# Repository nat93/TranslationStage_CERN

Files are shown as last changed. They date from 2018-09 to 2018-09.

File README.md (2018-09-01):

# TranslationStage_CERN
> Software for linear motorized stages developed at CERN for UA9 experiment. Graphic User Interface based on Matlab and Arduino code for microcontrollers. There are 3D drawings of the stages created in SolidWorks.

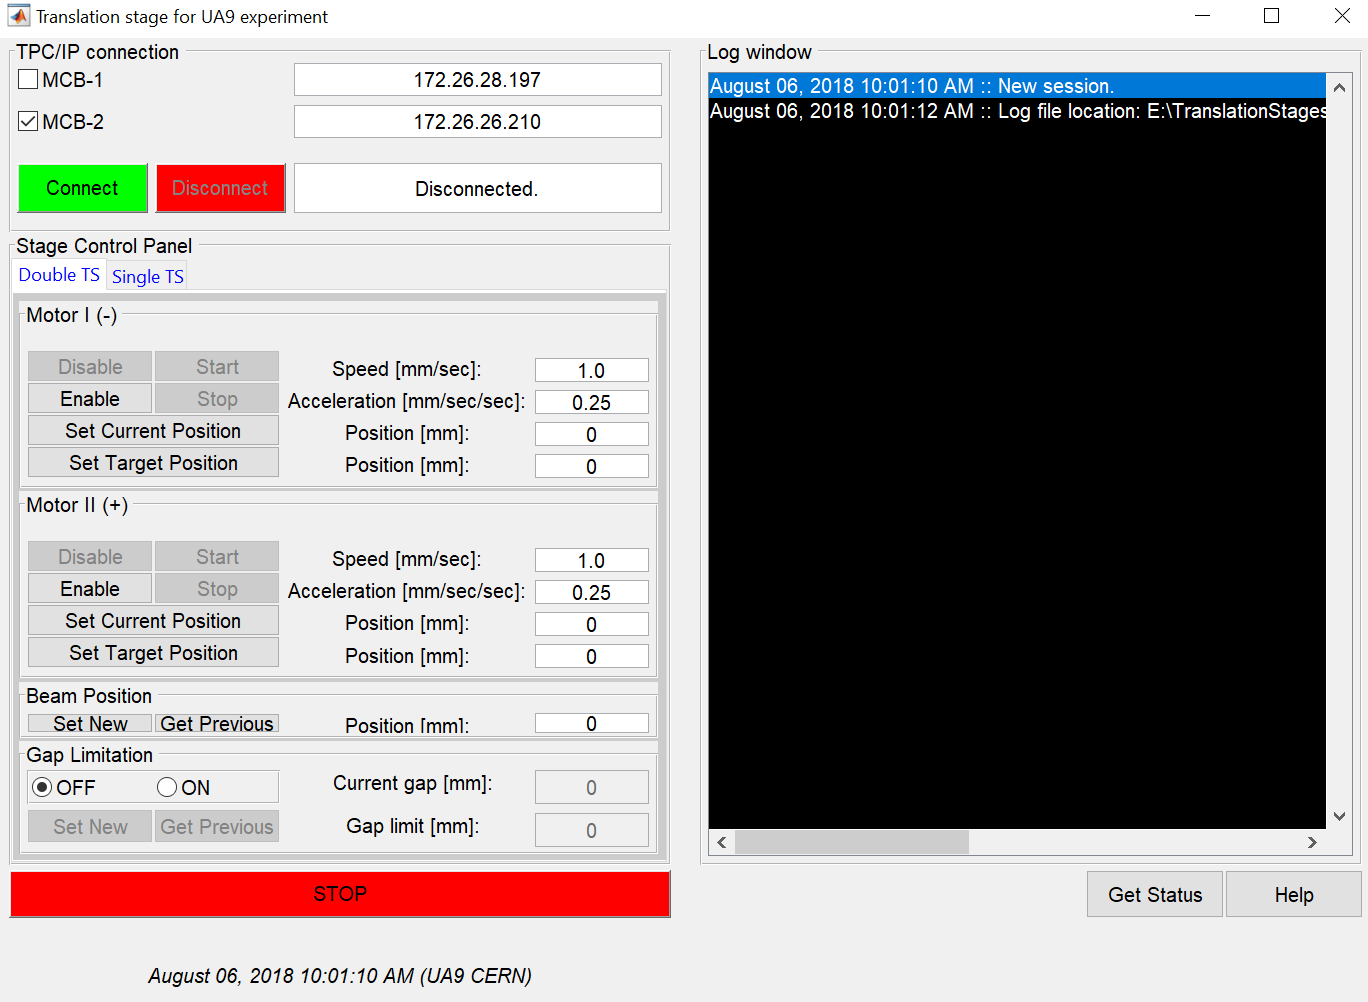
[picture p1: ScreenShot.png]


In recent times, an interest in the use of the bent crystals for the high-energy particle beam collimation and extraction has increased. A significant contribution to the technological progress of the development and installation such crystals at accelerators was made by the UA9 collaboration. So far an experimental work is carried out for the characterization of the crystals, their production and use on such accelerators as SPS or LHC at CERN. Nevertheless, before using the crystal for its intended purpose, it must be checked: determine the angle of the deflection, the efficiency of the channeling etc. Such tests are conducted at H8 SPS extraction beam line.

One of the important characteristics of the crystal is the probability of the inelastic nuclear interactions (INI) and its dependence on the crystal orientation with respect to the beam direction. To register the INI happening in the crystal a couple of plastic scintillators (10 × 25 × 5 mm3 ) is used in coincidences mode. For more effective INI events registration the position of the detectors should be symmetrical with respect to the center of the beam. 

Until 2017 the UA9 collaboration manually installed the plastic scintillators on the beam, each time interrupting the operation of the extraction line. This regime of the work was laborious and took a lot of experimental time. Thus, it was decided to create motorized linear platforms for moving the plastic scintillators with the possibility of remote control. In this case, physicists would not have to stop the work of the extraction line, and also remotely carry out calibration and alignment of the detectors with respect to the beam direction.

Description:
>> GUI_installer -- graphic user interface installation files for LINUX and WINDOWS operational systems.
>> TranslationStage_ARDUINO_SOURCE -- an Arduino based script for microcontroller.
>> TranslationStage_MATLAB_SOURCE -- a GUI script based on MATLAB.
>> TS-1 3D-CAD -- 3D model of the single translation stage.
>> TS-2 3D-CAD -- 3D model of the double translation stage.

Single Translation Stage:
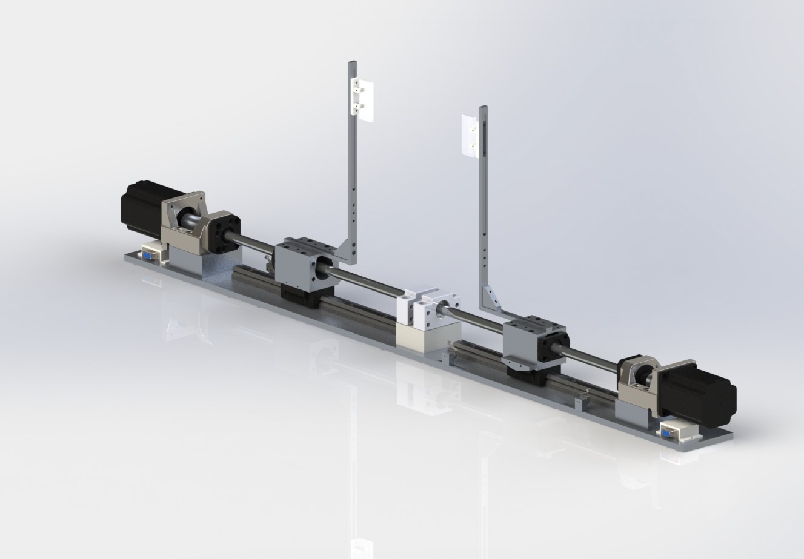
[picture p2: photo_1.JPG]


Double Translation Stage:
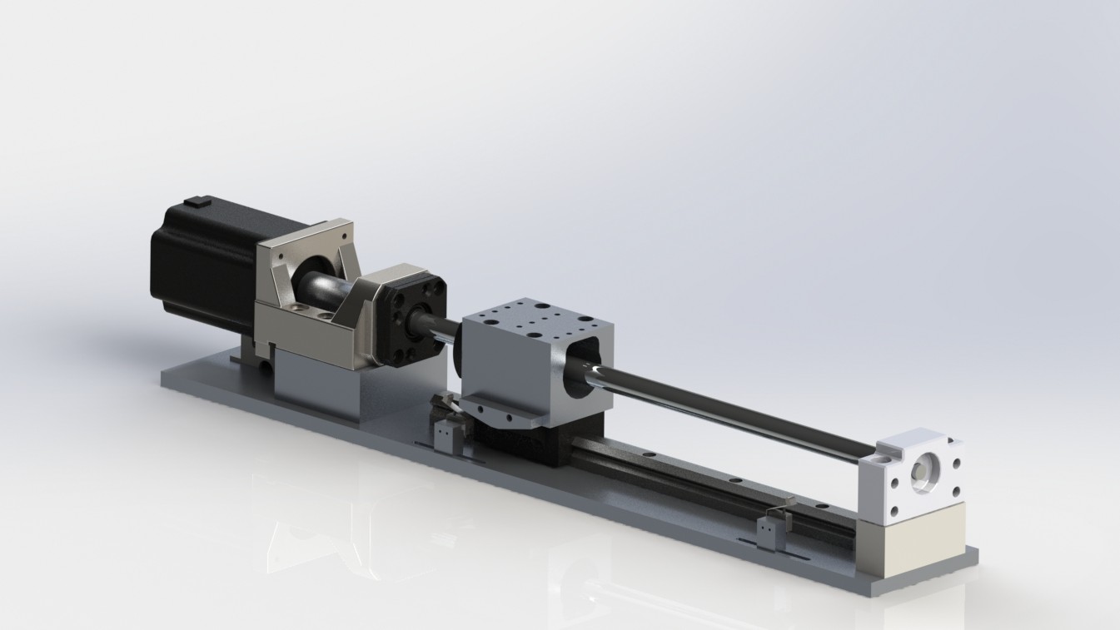
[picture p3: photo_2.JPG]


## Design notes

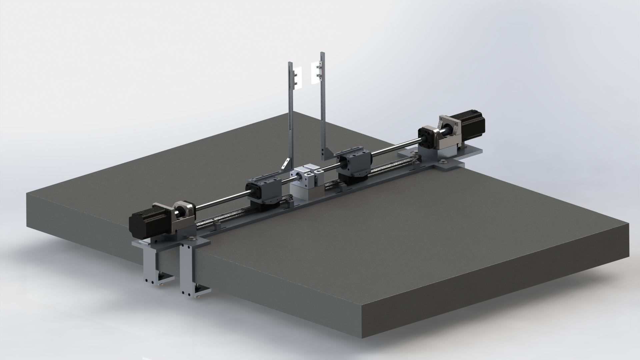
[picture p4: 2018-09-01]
TS-2 3D-CAD/pictures/photo.JPG

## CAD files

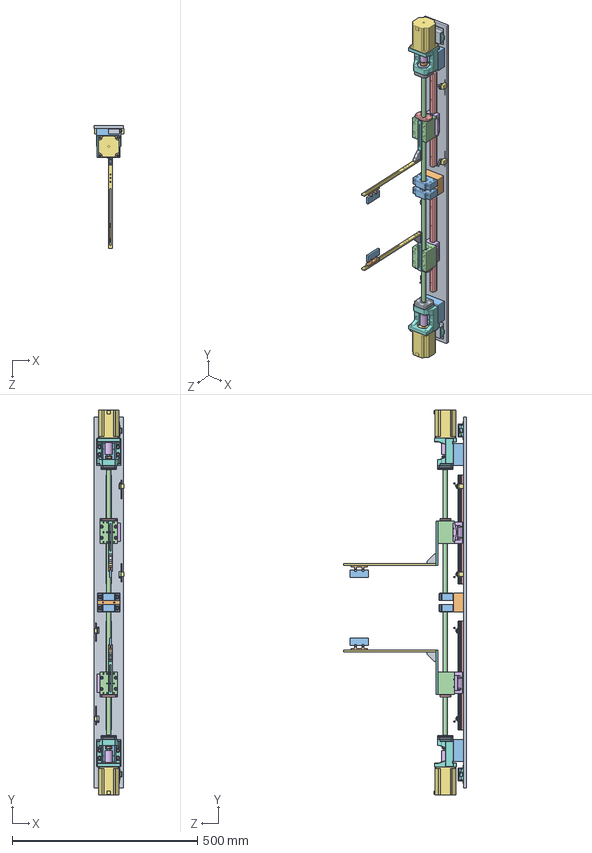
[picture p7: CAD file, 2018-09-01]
TS-2 3D-CAD/assembly.SLDASM
81.5 x 1038.2 x 332.0 mm
base_plate
support_1
BF10_C7 x 2
R1204_C7_ballscrew x 2
1204_FSKD x 2
BF_25D34L_Flexible_coupling x 2
NEMA23_SY57STH76_4004A x 2
MBA10-C x 2
FK10 x 2
FK101 x 2
support_2 x 2
holder_FSKD_R1204_2 x 2
rail_(BGR-15-LN) x 2
bearing_blocks(BGX-H-15-FN-ZF) x 2
holder_scintillator_1 x 2
holder_scintillator_2 x 2
for_CNC_6 x 2
holder_scintillator_3 x 2
scintillator x 2
switcher_hummer x 4
switcher_micro x 4
coner_switcher x 2
switcher_holder x 4
DB9_connector x 2
DB9_cover x 2

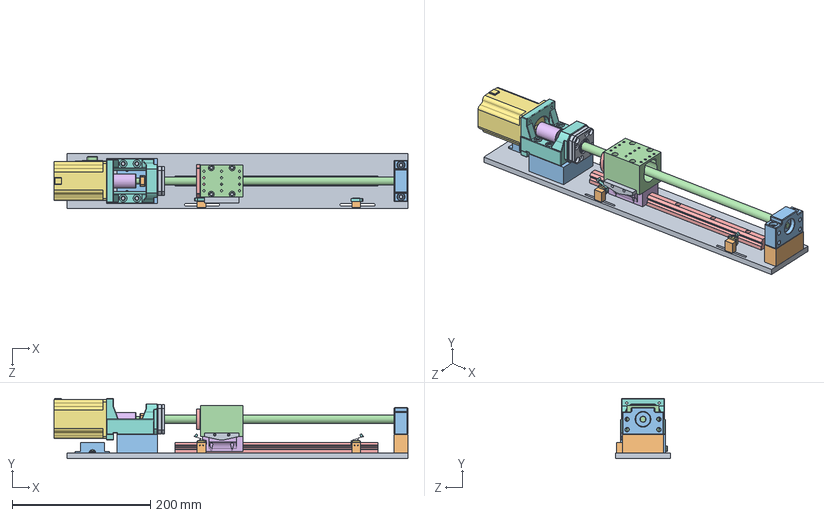
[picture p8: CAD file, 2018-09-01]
TS-1 3D-CAD/assembly.SLDASM
512.1 x 87.2 x 80.0 mm
base_plate
support_1
BF10_C7
R1204_C7_ballscrew
1204_FSKD
BF_25D34L_Flexible_coupling
NEMA23_SY57STH76_4004A
MBA10-C
FK10
FK101
support_2
holder_FSKD_R1204_2
rail_(BGR-15-LN)
bearing_blocks(BGX-H-15-FN-ZF)
switcher_micro x 2
switcher_hummer x 2
coner_switcher
switcher_holder x 2
DB9_cover
DB9_connector

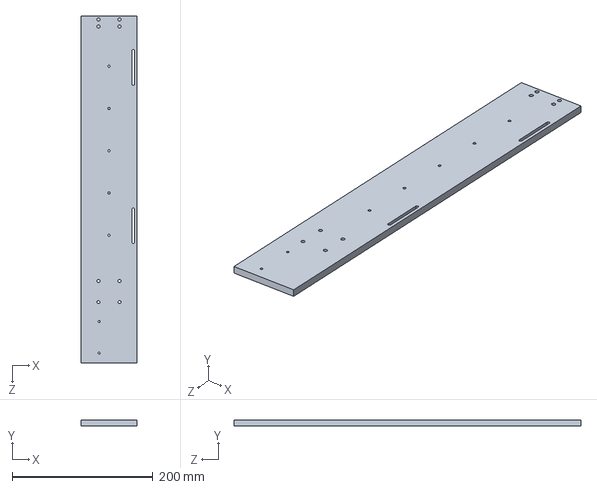
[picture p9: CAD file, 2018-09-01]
TS-1 3D-CAD/base_plate.SLDPRT
80.0 x 8.00 x 493.0 mm

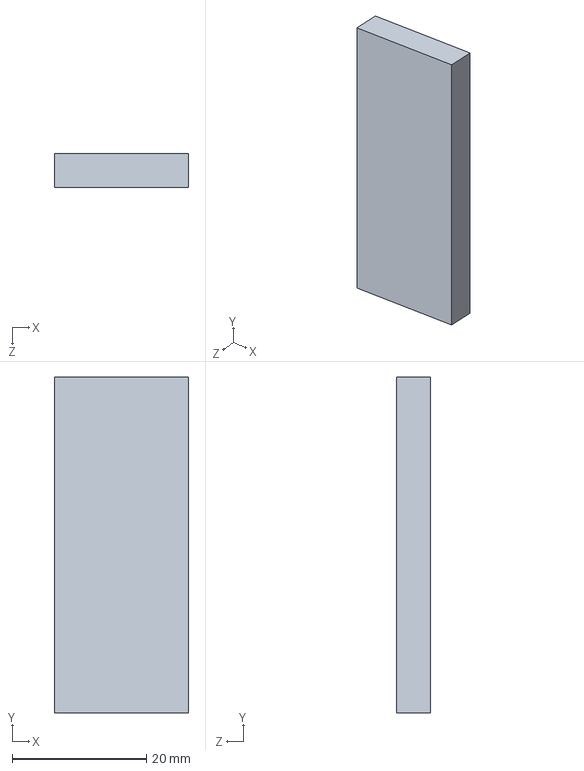
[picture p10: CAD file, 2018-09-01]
TS-2 3D-CAD/scintillator.SLDPRT
20.0 x 50.0 x 5.00 mm

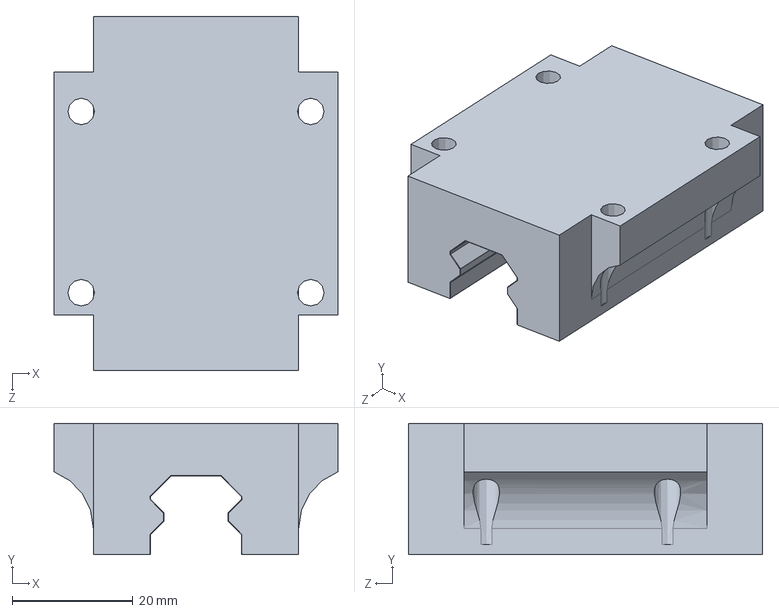
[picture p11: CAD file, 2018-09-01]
TS-1 3D-CAD/bearing_blocks(BGX-H-15-FN-ZF).SLDPRT
47.0 x 21.7 x 58.6 mm

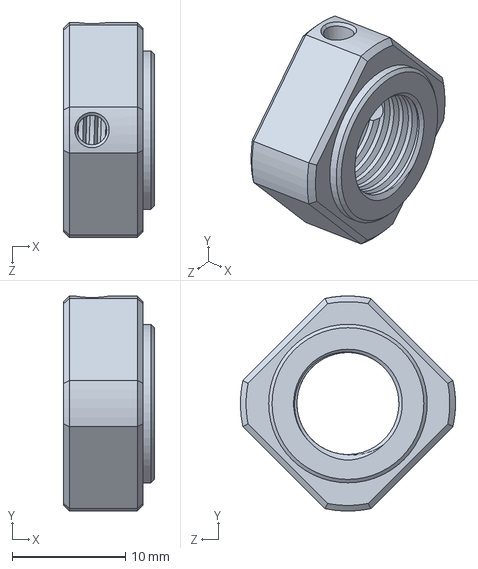
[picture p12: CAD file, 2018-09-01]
TS-1 3D-CAD/FK101.SLDPRT
8.00 x 19.0 x 19.0 mm

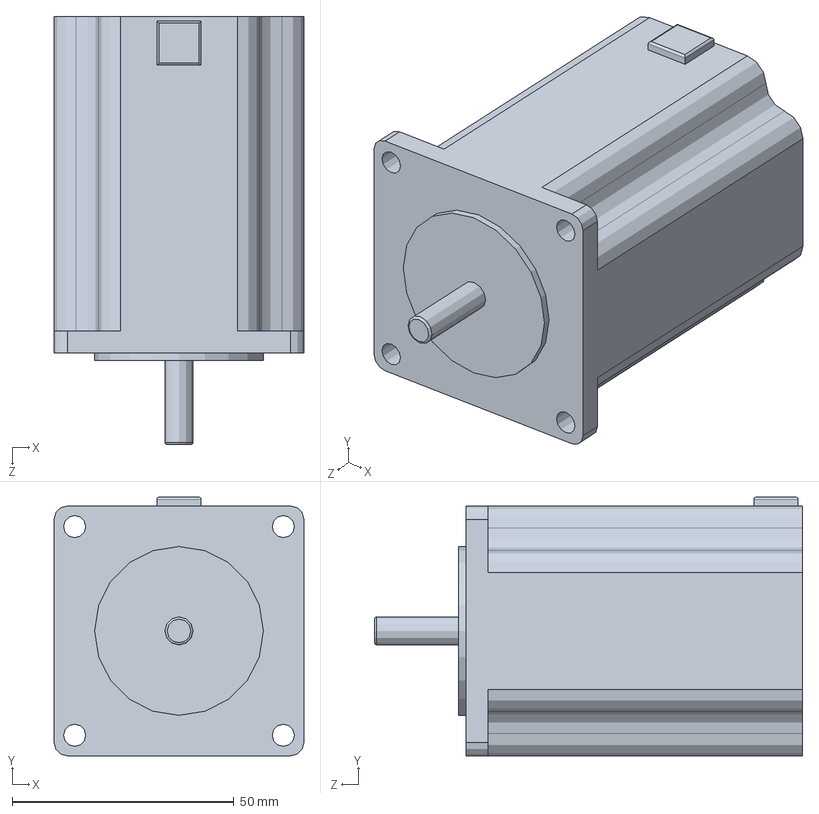
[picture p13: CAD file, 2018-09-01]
TS-2 3D-CAD/NEMA23_SY57STH76_4004A.SLDPRT
56.4 x 58.4 x 96.6 mm

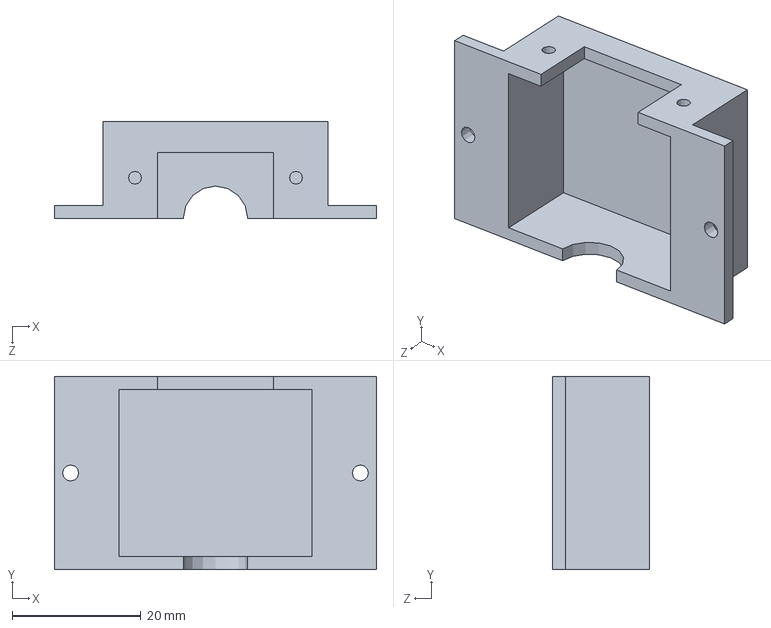
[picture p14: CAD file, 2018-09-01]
TS-1 3D-CAD/DB9_cover.SLDPRT
50.0 x 30.0 x 15.0 mm

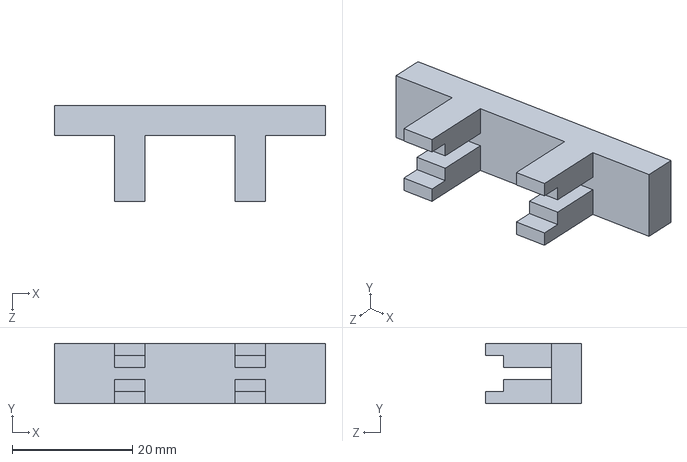
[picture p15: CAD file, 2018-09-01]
TS-2 3D-CAD/for_3d_printer_2.SLDPRT
45.0 x 10.0 x 16.0 mm

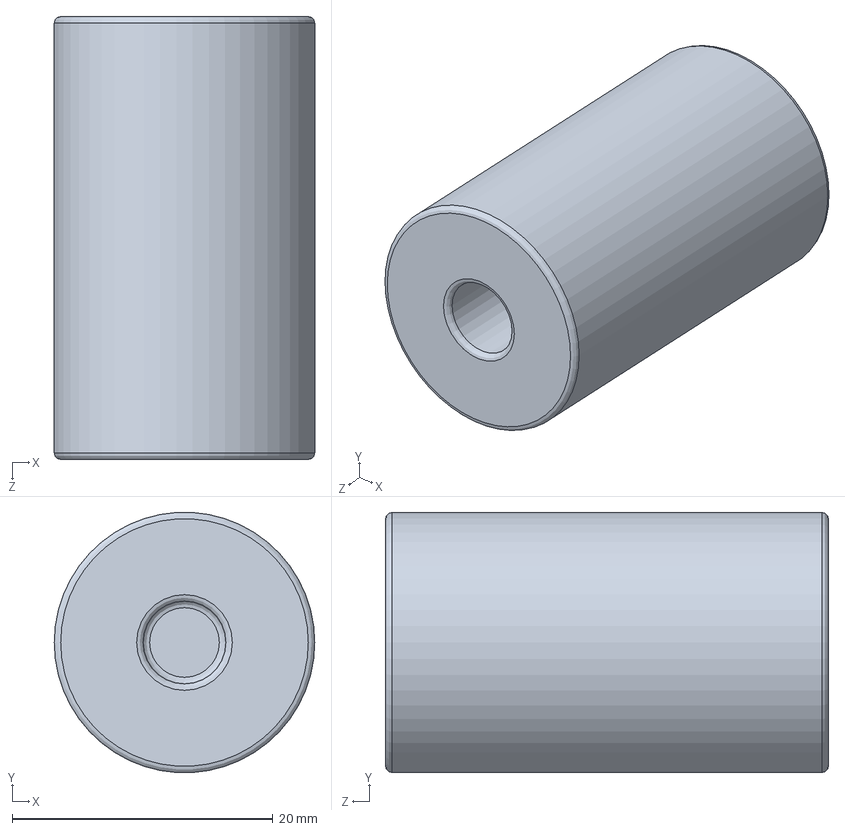
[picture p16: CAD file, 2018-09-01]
TS-1 3D-CAD/BF_25D34L_Flexible_coupling.SLDPRT
20.0 x 20.0 x 34.0 mm

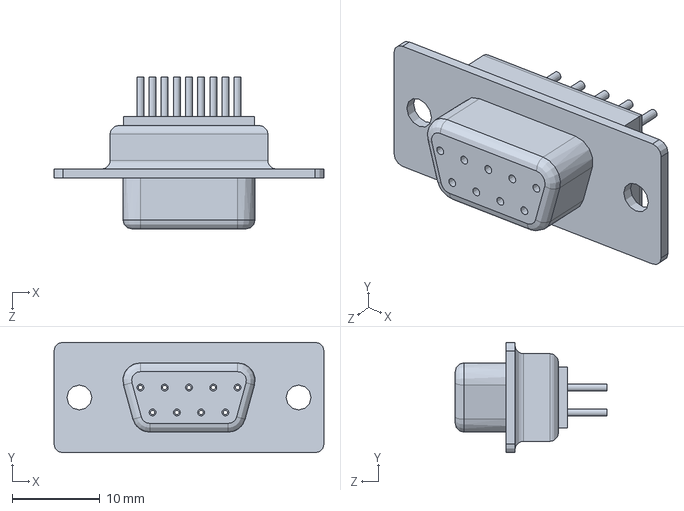
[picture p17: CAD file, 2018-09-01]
TS-2 3D-CAD/DB9_connector.SLDPRT
30.8 x 12.6 x 17.3 mm

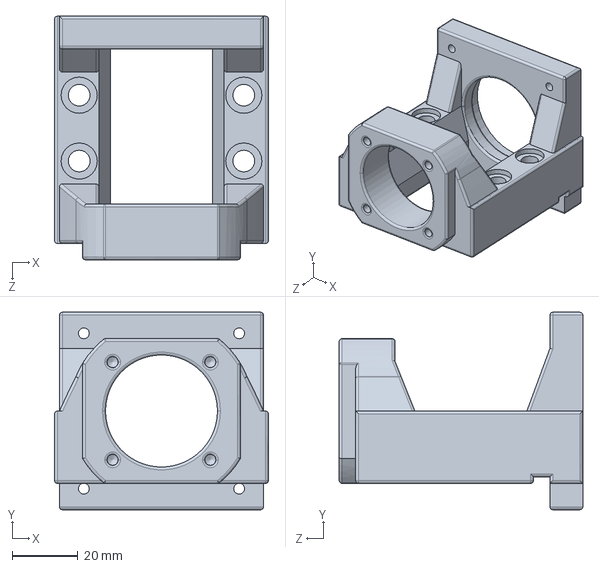
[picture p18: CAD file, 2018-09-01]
TS-1 3D-CAD/MBA10-C.SLDPRT
65.0 x 60.0 x 74.0 mm

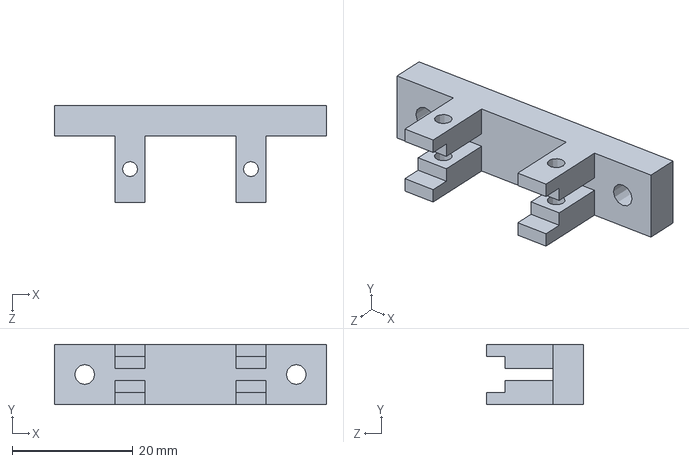
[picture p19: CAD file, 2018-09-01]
TS-2 3D-CAD/holder_scintillator_3.SLDPRT
45.0 x 10.0 x 16.0 mm

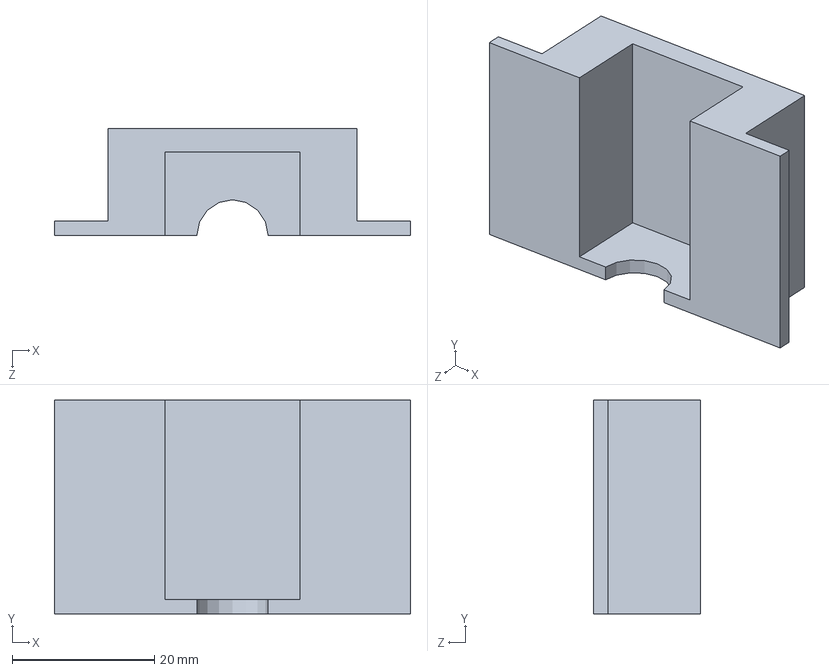
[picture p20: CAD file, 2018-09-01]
TS-2 3D-CAD/for_3d_printer_1.SLDPRT
50.0 x 30.0 x 15.0 mm

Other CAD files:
TS-1 3D-CAD/Electrical_2-assembly.sldasm
TS-1 3D-CAD/Cable_1-assembly.sldasm
TS-2 3D-CAD/bearing_blocks(BGX-H-15-FN-ZF).SLDPRT
TS-1 3D-CAD/fixator_2.SLDPRT
TS-1 3D-CAD/1204_FSKD.SLDPRT
TS-1 3D-CAD/BF10_C7.SLDPRT
TS-1 3D-CAD/DB9 female connector.SLDPRT
TS-1 3D-CAD/DB9_connector.SLDPRT
TS-1 3D-CAD/FK10.SLDPRT
TS-1 3D-CAD/NEMA23_SY57STH76_4004A.SLDPRT
TS-1 3D-CAD/R1204_C7_ballscrew.SLDPRT
TS-1 3D-CAD/WorkShop/base_plate.SLDDRW
TS-1 3D-CAD/WorkShop/holder_FSKD_R1204_2.SLDDRW
TS-1 3D-CAD/WorkShop/support_1.SLDDRW
TS-1 3D-CAD/WorkShop/support_2.SLDDRW
TS-1 3D-CAD/assembly.SLDDRW
TS-1 3D-CAD/coner_switcher.SLDPRT
TS-1 3D-CAD/fixator_1.SLDPRT
TS-1 3D-CAD/fixator_3.SLDPRT
TS-1 3D-CAD/fixator_4.SLDPRT
TS-1 3D-CAD/for_CNC_6.SLDPRT
TS-1 3D-CAD/granite_table.SLDPRT
TS-1 3D-CAD/holder_FSKD_R1204_2.SLDPRT
TS-1 3D-CAD/holder_scintillator_1.SLDPRT
TS-1 3D-CAD/holder_scintillator_2.SLDPRT
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

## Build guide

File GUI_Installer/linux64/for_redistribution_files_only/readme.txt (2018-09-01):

MATLAB Compiler

1. Prerequisites for Deployment 

. Verify the MATLAB Runtime is installed and ensure you    
  have installed version 9.1 (R2016b).   

. If the MATLAB Runtime is not installed, do the following:
  (1) enter
  
      >>mcrinstaller
      
      at MATLAB prompt. The MCRINSTALLER command displays the 
      location of the MATLAB Runtime installer.

  (2) run the MATLAB Runtime installer.

Or download the Linux 64-bit version of the MATLAB Runtime for R2016b 
from the MathWorks Web site by navigating to

   http://www.mathworks.com/products/compiler/mcr/index.html

For more information about the MATLAB Runtime and the MATLAB Runtime installer, see 
Package and Distribute in the MATLAB Compiler documentation  
in the MathWorks Documentation Center.    

2. Files to Deploy and Package

Files to package for Standalone 
================================
-TranslationStageCERN 
-run_TranslationStageCERN.sh (shell script for temporarily setting environment variables 
                              and executing the application)
   -to run the shell script, type
   
       ./run_TranslationStageCERN.sh <mcr_directory> <argument_list>
       
    at Linux or Mac command prompt. <mcr_directory> is the directory 
    where version 9.1 of the MATLAB Runtime is installed or the directory where 
    MATLAB is installed on the machine. <argument_list> is all the 
    arguments you want to pass to your application. For example, 

    If you have version 9.1 of the MATLAB Runtime installed in 
    /mathworks/home/application/v91, run the shell script as:
    
       ./run_TranslationStageCERN.sh /mathworks/home/application/v91
       
    If you have MATLAB installed in /mathworks/devel/application/matlab, 
    run the shell script as:
    
       ./run_TranslationStageCERN.sh /mathworks/devel/application/matlab
-MCRInstaller.zip
   -if end users are unable to download the MATLAB Runtime using the above  
    link, include it when building your component by clicking 
    the "Runtime downloaded from web" link in the Deployment Tool
-This readme file 

3. Definitions

For information on deployment terminology, go to 
http://www.mathworks.com/help. Select MATLAB Compiler >   
Getting Started > About Application Deployment > 
Deployment Product Terms in the MathWorks Documentation 
Center.

4. Appendix 

A. Linux x86-64 systems:
In the following directions, replace MCR_ROOT by the directory where the MATLAB Runtime 
   is installed on the target machine.

(1) Set the environment variable XAPPLRESDIR to this value:

    MCR_ROOT/v91/X11/app-defaults

(2) If the environment variable LD_LIBRARY_PATH is undefined, set it to the concatenation 
   of the following strings:

    MCR_ROOT/v91/runtime/glnxa64:
    MCR_ROOT/v91/bin/glnxa64:
    MCR_ROOT/v91/sys/os/glnxa64:
    MCR_ROOT/v91/sys/opengl/lib/glnxa64

    If it is defined, set it to the concatenation of these strings:

    ${LD_LIBRARY_PATH}: 
    MCR_ROOT/v91/runtime/glnxa64:
    MCR_ROOT/v91/bin/glnxa64:
    MCR_ROOT/v91/sys/os/glnxa64:
    MCR_ROOT/v91/sys/opengl/lib/glnxa64

   For more detail information about setting the MATLAB Runtime paths, see Package and 
   Distribute in the MATLAB Compiler documentation in the MathWorks Documentation Center.

        NOTE: To make these changes persistent after logout on Linux 
              or Mac machines, modify the .cshrc file to include this  
              setenv command.
        NOTE: The environment variable syntax utilizes forward 
              slashes (/), delimited by colons (:).  
        NOTE: When deploying standalone applications, it is possible 
              to run the shell script file run_TranslationStageCERN.sh 
              instead of setting environment variables. See 
              section 2 "Files to Deploy and Package".

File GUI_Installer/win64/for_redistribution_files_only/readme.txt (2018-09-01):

MATLAB Compiler

1. Prerequisites for Deployment 

. Verify the MATLAB Runtime is installed and ensure you    
  have installed version 9.0.1 (R2016a).   

. If the MATLAB Runtime is not installed, do the following:
  (1) enter
  
      >>mcrinstaller
      
      at MATLAB prompt. The MCRINSTALLER command displays the 
      location of the MATLAB Runtime installer.

  (2) run the MATLAB Runtime installer.

Or download the Windows 64-bit version of the MATLAB Runtime for R2016a 
from the MathWorks Web site by navigating to

   http://www.mathworks.com/products/compiler/mcr/index.html

For more information about the MATLAB Runtime and the MATLAB Runtime installer, see 
Package and Distribute in the MATLAB Compiler documentation  
in the MathWorks Documentation Center.    

NOTE: You will need administrator rights to run MCRInstaller. 

2. Files to Deploy and Package

Files to package for Standalone 
================================
-TranslationStageCERN.exe
-MCRInstaller.exe 
   -if end users are unable to download the MATLAB Runtime using the above  
    link, include it when building your component by clicking 
    the "Runtime downloaded from web" link in the Deployment Tool
-This readme file 

3. Definitions

For information on deployment terminology, go to 
http://www.mathworks.com/help. Select MATLAB Compiler >   
Getting Started > About Application Deployment > 
Deployment Product Terms in the MathWorks Documentation 
Center.

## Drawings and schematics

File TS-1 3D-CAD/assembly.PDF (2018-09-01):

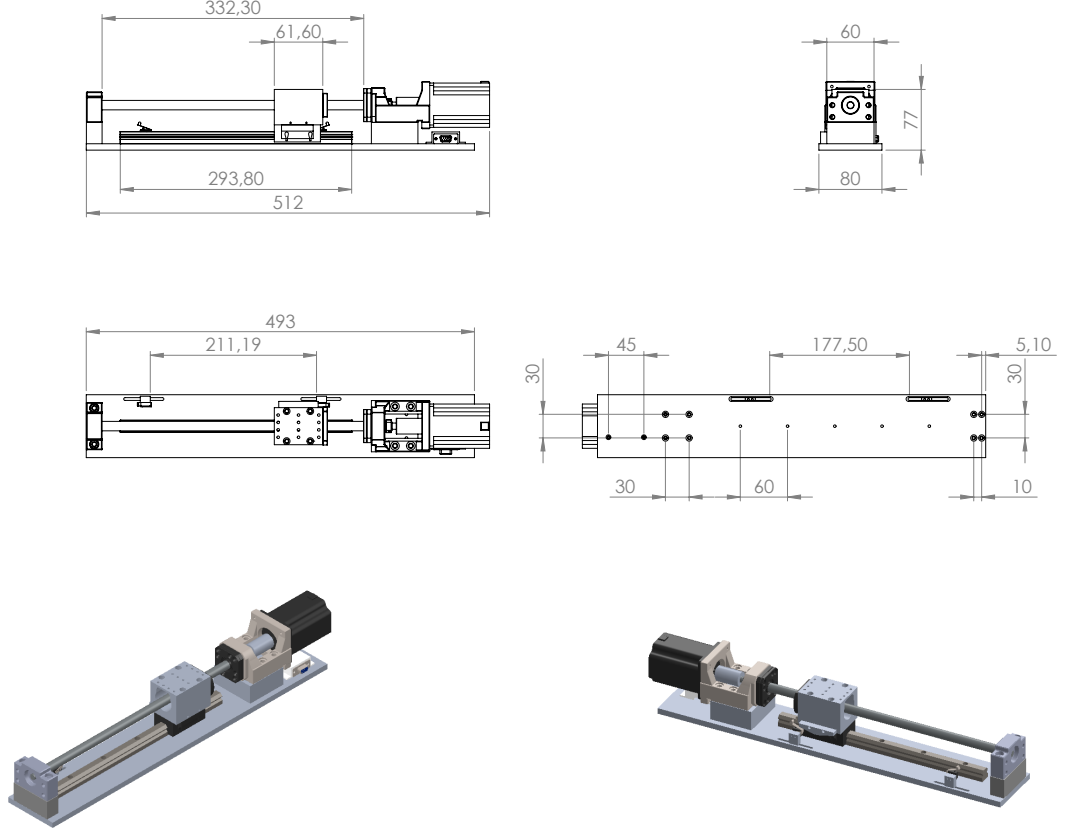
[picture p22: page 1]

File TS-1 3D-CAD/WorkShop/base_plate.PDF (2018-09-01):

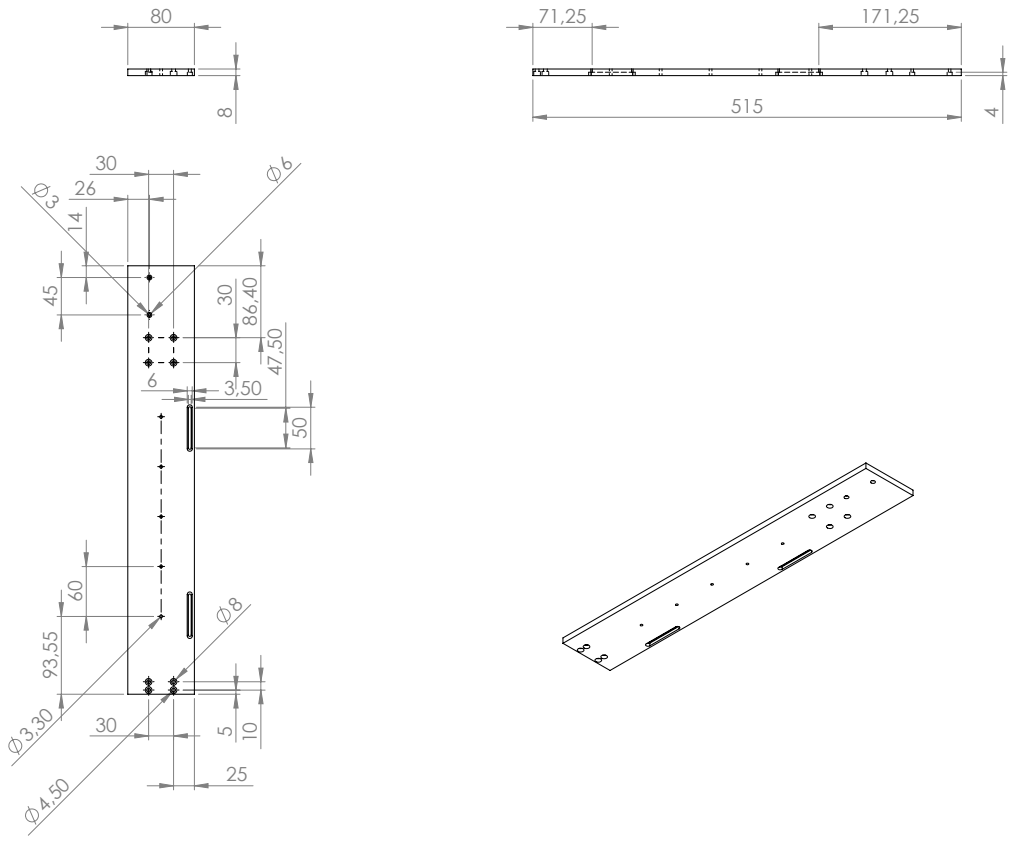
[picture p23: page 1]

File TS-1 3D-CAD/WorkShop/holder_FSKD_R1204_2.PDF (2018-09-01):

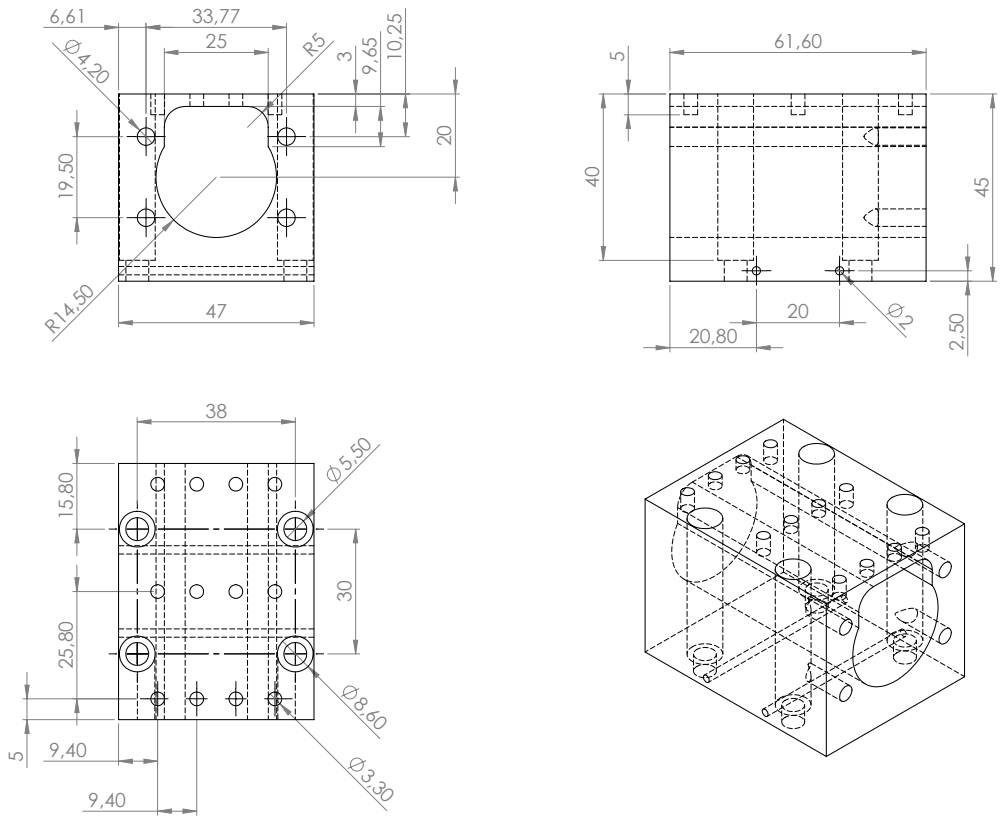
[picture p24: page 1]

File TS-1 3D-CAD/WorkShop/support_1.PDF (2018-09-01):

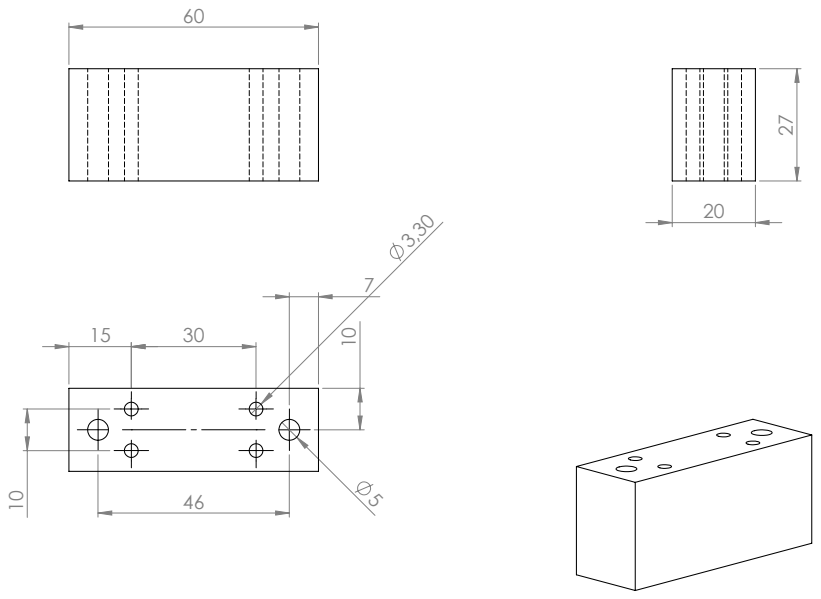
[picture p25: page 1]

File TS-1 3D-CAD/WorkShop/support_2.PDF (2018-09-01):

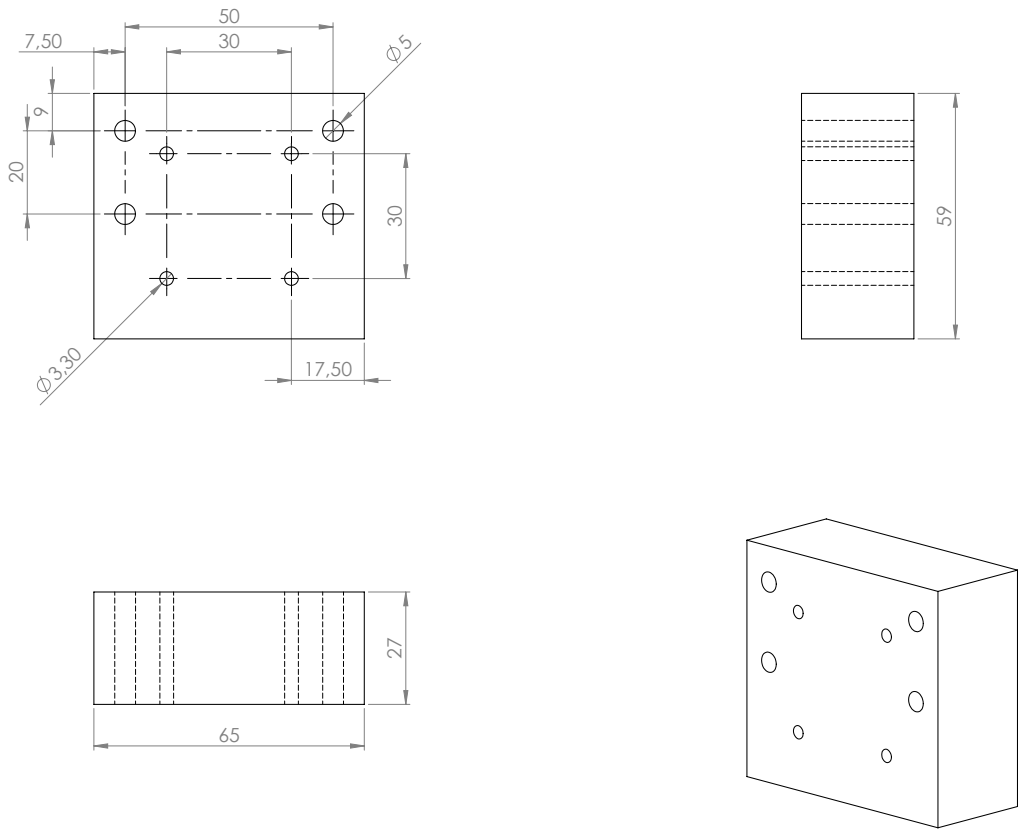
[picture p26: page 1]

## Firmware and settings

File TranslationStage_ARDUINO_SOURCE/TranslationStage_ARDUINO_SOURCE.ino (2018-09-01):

//--------------------------------------------------------------------------------//
//---------  Andrii Natochii  ------  CERN 2018  ---------------------------------//
//------------  e-mail: andrii.natochii@cern.ch  ---------------------------------//
//--------------------------------------------------------------------------------//
//--------------------------------------------------------------------------------//
//You have been allocated to the following IP address:
//IPv4[172.26.28.197]
//for interface LALARDUETH01 of device LALARDUETH01 connected on outlet 0887-R:2004/02.
//
//The following setting may also need to be configured your IPv4 network connection:
//Default gateway: 172.26.28.1
//Subnet mask: 255.255.255.0
//Broadcast address: 172.26.28.255 
//DNS servers: 137.138.16.5 and 137.138.17.5
//Time servers: 137.138.16.69, 137.138.17.69 and 137.138.18.69
//--------------------------------------------------------------------------------//
//--------------------------------------------------------------------------------//
//You have been allocated to the following IP address:
//IPv4[172.26.26.210]
//for interface LALARDUETH02 of device LALARDUETH02 connected on outlet 0887-R:2004/01.
//
//The following setting may also need to be configured your IPv4 network connection:
//Default gateway: 172.26.26.1
//Subnet mask: 255.255.255.0
//Broadcast address: 172.26.26.255 
//DNS servers: 137.138.16.5 and 137.138.17.5
//Time servers: 137.138.16.69, 137.138.17.69 and 137.138.18.69
//--------------------------------------------------------------------------------//
//--------------------------------------------------------------------------------//

#include <SPI.h>
#include <Ethernet2.h>
#include <AccelStepper.h>
#include <TimerOne.h>
//--------------------------------------------------------------------------------//
#define TIMER_US 100                                // 50mkS set timer duration in microseconds. 
volatile bool in_long_isr = false; 
boolean RunMotorStatus = false;                    // Boolean variable for running motors
                                                   // with period 2*TIMER_US
//--------------------------------------------------------------------------------//
//Ethernet Default Settings

byte mac[] = {0x90,0xA2,0xDA,0x10,0x76,0xFE};       // MAC address for the LALARDUETH01
IPAddress ip(172,26,28,197);                        // Default ip.

//byte mac[] = {0x90,0xA2,0xDA,0x0F,0x8B,0x0E};       // MAC address for the LALARDUETH02
//IPAddress ip(172,26,26,210);                        // Default ip.

EthernetServer server(80);                          // Default server.
EthernetClient client;                              // Object of EthernetClient class.
boolean reading = false;                            // Boolean variable.
String userString;                                  // Buffer of user command.
const int deselectSDpin = 4;                        // Pin fro deselecting SD card.
//--------------------------------------------------------------------------------//
//Switcher
const int SW11pin = A1;                             // Pin A1 of Arduino board - read switcher 11 (Motor1).
const int SW12pin = A2;                             // Pin A2 of Arduino board - read switcher 12 (Motor1).
const int SW21pin = A4;                             // Pin A4 of Arduino board - read switcher 21 (Motor2).
const int SW22pin = A3;                             // Pin A3 of Arduino board - read switcher 22 (Motor2).
const int SW31pin = A5;                             // Pin A5 of Arduino board - read switcher 31 (Motor3).
const int SW32pin = A0;                             // Pin A0 of Arduino board - read switcher 32 (Motor3).
int SW11st = 1;                                     // Status of the switcher 11.
int SW12st = 1;                                     // Status of the switcher 12.
int SW21st = 1;                                     // Status of the switcher 21.
int SW22st = 1;                                     // Status of the switcher 22.
int SW31st = 1;                                     // Status of the switcher 31.
int SW32st = 1;                                     // Status of the switcher 32.
                                                    // 1 - switcher is not pressed.
                                                    // 0 - switcher is pressed.
//--------------------------------------------------------------------------------//
//Motor1 Default Settings
AccelStepper stepper1(1,3,8);                       // First obj of AccelStepper class. A stepper motor controlled by a dedicated driver board.
                                                    // 3 - Pin 3 of Arduino board 
                                                    // - Step pin ;
                                                    // 8 - Pin 8 of Arduino board
                                                    // - Direction pin.
int long M1_speed = 0;                              // Steps per second.
int long M1_acc = 0;                                // Steps per second per second.
int long M1_dist = 0;                               // Distance in Steps.
int long M1_curpos = 0;                             // Current position in steps.
int long M1_targpos = 0;                            // Target position in steps.
boolean M1_ena = false;                             // Flag DISABLE.
boolean M1_move = false;                            // Flag MOVING.
//--------------------------------------------------------------------------------//
//Motor2 Default Settings
AccelStepper stepper2(1,5,9);                       // Second obj of AccelStepper class. A stepper motor controlled by a dedicated driver board.
                                                    // 5 - Pin 5 of Arduino board 
                                                    // - Step pin ;
                                                    // 9 - Pin 9 of Arduino board
                                                    // - Direction pin.
int long M2_speed = 0;                              // Steps per second.
int long M2_acc = 0;                                // Steps per second per second.
int long M2_dist = 0;                               // Distance in Steps.
int long M2_curpos = 0;                             // Current position in steps.
int long M2_targpos = 0;                            // Target position in steps.
boolean M2_ena = false;                             // Flag DISABLE.
boolean M2_move = false;                            // Flag MOVING.
//--------------------------------------------------------------------------------//
//Motor3 Default Settings
AccelStepper stepper3(1,7,6);                       // Second obj of AccelStepper class. A stepper motor controlled by a dedicated driver board.
                                                    // 7 - Pin 7 of Arduino board 
                                                    // - Step pin ;
                                                    // 6 - Pin 6 of Arduino board
                                                    // - Direction pin.
int long M3_speed = 0;                              // Steps per second.
int long M3_acc = 0;                                // Steps per second per second.
int long M3_dist = 0;                               // Distance in Steps.
int long M3_curpos = 0;                             // Current position in steps.
int long M3_targpos = 0;                            // Target position in steps.
boolean M3_ena = false;                             // Flag DISABLE.
boolean M3_move = false;                            // Flag MOVING.
//--------------------------------------------------------------------------------//
const int ENApin = 2;                              // Pin 2 - Enabling pin.
//--------------------------------------------------------------------------------//
// Setup function
void setup()
{
  //Serial.begin(9600);
  //--------------------------------------------------------------------------------//
  //Switcher
  pinMode(SW11pin, INPUT_PULLUP);
  pinMode(SW12pin, INPUT_PULLUP);
  pinMode(SW21pin, INPUT_PULLUP);
  pinMode(SW22pin, INPUT_PULLUP);
  pinMode(SW31pin, INPUT_PULLUP);
  pinMode(SW32pin, INPUT_PULLUP);
  //--------------------------------------------------------------------------------//
  //Ethernet Shield
  pinMode(deselectSDpin, OUTPUT);                    // Set like output pin 4 to deselect SD card.
  digitalWrite(deselectSDpin, HIGH);
  //--------------------------------------------------------------------------------//
  //Motors1 setup
  stepper1.setMinPulseWidth(20);                     // Set the minimum pulse width allowed
                                                     // by the stepper driver. The minimum 
                                                     // practical pulse width is approximately 
                                                     // 20 microseconds. Times less than 20 
                                                     // microseconds will usually result in 
                                                     // 20 microseconds or so.
  stepper1.setCurrentPosition(M1_curpos);            // Resets the current position of the 
                                                     // motor, so that wherever the motor 
                                                     // happens to be right now is considered 
                                                     // to be the new 0 position. 
                                                     // Useful for setting a zero position on 
                                                     // a stepper after an initial hardware 
                                                     // positioning move. Has the side effect 
                                                     // of setting the current motor speed to 0.
  //--------------------------------------------------------------------------------//
  //Motors2 setup
  stepper2.setMinPulseWidth(20);                     // Set the minimum pulse width allowed
                                                     // by the stepper driver. The minimum 
                                                     // practical pulse width is approximately 
                                                     // 20 microseconds. Times less than 20 
                                                     // microseconds will usually result in 
                                                     // 20 microseconds or so.
  stepper2.setCurrentPosition((-1)*M2_curpos);       // Resets the current position of the 
                                                     // motor, so that wherever the motor 
                                                     // happens to be right now is considered 
                                                     // to be the new 0 position. 
                                                     // Useful for setting a zero position on 
                                                     // a stepper after an initial hardware 
                                                     // positioning move. Has the side effect 
                                                     // of setting the current motor speed to 0.
  //--------------------------------------------------------------------------------//
  //Motors3 setup
  stepper3.setMinPulseWidth(20);                     // Set the minimum pulse width allowed
                                                     // by the stepper driver. The minimum 
                                                     // practical pulse width is approximately 
                                                     // 20 microseconds. Times less than 20 
                                                     // microseconds will usually result in 
                                                     // 20 microseconds or so.
  stepper3.setCurrentPosition(M3_curpos);            // Resets the current position of the 
                                                     // motor, so that wherever the motor 
                                                     // happens to be right now is considered 
                                                     // to be the new 0 position. 
                                                     // Useful for setting a zero position on 
                                                     // a stepper after an initial hardware 
                                                     // positioning move. Has the side effect 
                                                     // of setting the current motor speed to 0.                                                     
  //--------------------------------------------------------------------------------//
  pinMode(ENApin, OUTPUT);                          // Set ENApin as output. 
  digitalWrite(ENApin, LOW);                        // Disable motors.
  //--------------------------------------------------------------------------------//
  //Ethernet connection setup
  Ethernet.begin(mac, ip);                           // Initializes the ethernet library 
                                                     // and network settings.
  server.begin();                                    // Start listening for clients. 
  //--------------------------------------------------------------------------------//
  Timer1.initialize(TIMER_US);                       // Initialize timer1, and set a TIMER_US
                                                     // microseconds period.
  Timer1.attachInterrupt( timerIsr );                // Attaches timerIsr() as a timer overflow 
                                                     // interrupt.
  //--------------------------------------------------------------------------------//
}
//--------------------------------------------------------------------------------//
// Main loop
void loop()
{   
  //--------------------------------------------------------------------------------//
  userString = "";                                   // Clearning user command buffer.
  client = server.available();                       // If an incoming client connects, 
                                                     // there will be bytes available to 
                                                     // read.
  if (client)
  {
    CheckClient();                                   // Read and check client command
  }
  /*if(userString != "")
  {
    Serial.println(userString);
  }*/
  //--------------------------------------------------------------------------------//
}
//--------------------------------------------------------------------------------//
// Interrupt function
void timerIsr()
{
  //--------------------------------------------------------------------------------//
  if (in_long_isr)
  {
    return;
  }
  in_long_isr = true;
  interrupts();                                     // Start interrupt
  //--------------------------------------------------------------------------------//
  if(RunMotorStatus)
  {
    RunMotors();
  }
  RunMotorStatus = !RunMotorStatus;                // We use double period.
  //--------------------------------------------------------------------------------//
  // Check Switcher
  SW11st = 0;
  SW12st = 0;
  SW21st = 0;
  SW22st = 0;
  SW31st = 0;
  SW32st = 0;
  
  for(int i = 0; i < 10; i ++)
  {
    SW11st += abs(digitalRead(SW11pin));                   // Read input pin for switcher 11.
    SW12st += abs(digitalRead(SW12pin));                   // Read input pin for switcher 12.
    SW21st += abs(digitalRead(SW21pin));                   // Read input pin for switcher 21.
    SW22st += abs(digitalRead(SW22pin));                   // Read input pin for switcher 22.
    SW31st += abs(digitalRead(SW31pin));                   // Read input pin for switcher 31.
    SW32st += abs(digitalRead(SW32pin));                   // Read input pin for switcher 32.
  }
  
  M1_curpos = stepper1.currentPosition();
  M2_curpos = (-1)*stepper2.currentPosition();
  M3_curpos = stepper3.currentPosition();
  
  if(SW11st == 0 && M1_targpos < M1_curpos)
  {
    M1_move = false;
    M1_targpos = M1_curpos;
    stepper1.stop();
  }
  if(SW12st == 0 && M1_targpos > M1_curpos)
  {
    M1_move = false;
    M1_targpos = M1_curpos;
    stepper1.stop();  
  }
  if(SW21st == 0 && M2_targpos < M2_curpos)
  {
    M2_move = false;
    M2_targpos = M2_curpos;
    stepper2.stop(); 
  }
  if(SW22st == 0 && M2_targpos > M2_curpos)
  {
    M2_move = false;    
    M2_targpos = M2_curpos;
    stepper2.stop(); 
  }
  if(SW31st == 0 && M3_targpos < M3_curpos)
  {
    M3_move = false;
    M3_targpos = M3_curpos;
    stepper3.stop();
  }
  if(SW32st == 0 && M3_targpos > M3_curpos)
  {
    M3_move = false;
    M3_targpos = M3_curpos;
    stepper3.stop();  
  }
  //--------------------------------------------------------------------------------//
  noInterrupts();                                   // Stop interrupt
  in_long_isr = false;
  //--------------------------------------------------------------------------------//
}
//--------------------------------------------------------------------------------//
void RunMotors()
{
  //--------------------------------------------------------------------------------//
  // Motor1
  if(M1_move && M1_ena && M1_speed > 0)            // Check motor 1 flags
  {    
    stepper1.run();                                // Run motor 1
  }
  else
  {
    stepper1.stop();                               // Stop motor 1 as fast as possible: sets new target.
    M1_curpos = stepper1.currentPosition();
    stepper1.setCurrentPosition(M1_curpos);
  }  
  //--------------------------------------------------------------------------------//
  //Motor2
  if(M2_move && M2_ena && M2_speed > 0)            // Check motor 2 flags
  {
    stepper2.run();                                // Run motor 2
  }
  else
  {
    stepper2.stop();                               // Stop motor 2 as fast as possible: sets new target.
    M2_curpos = (-1)*stepper2.currentPosition();
    stepper2.setCurrentPosition((-1)*M2_curpos);
  } 
  //--------------------------------------------------------------------------------//
  // Motor3
  if(M3_move && M3_ena && M3_speed > 0)            // Check motor 3 flags
  {    
    stepper3.run();                                // Run motor 3
  }
  else
  {
    stepper3.stop();                               // Stop motor 3 as fast as possible: sets new target.
    M3_curpos = stepper3.currentPosition();
    stepper3.setCurrentPosition(M3_curpos);
  }  
}
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
